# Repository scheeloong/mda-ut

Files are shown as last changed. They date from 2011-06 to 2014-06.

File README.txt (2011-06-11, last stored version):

Directory: root
Use: Holds everything that needs to be held
Author: Mark Harfouche
Editors:

This directory holds all the other directories.
It also has a makefile that, for the sake that if things change

Changes directories, and compiles everything appropriatly.

Things should be compiled in the following order:

SOPC
FPGA
BSP
NIOS2 CODE

VISION

JOYSTICK

...

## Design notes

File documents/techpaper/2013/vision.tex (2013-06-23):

\section{Software}

The vision subsystem is a critical component of AquaTux because it is
the one performing the identification of mission objectives. It is
also complementary to the passive sonar to grab the suitcase above the
acoustic pinger. Because the turbidity of the water and the small
number of visual features in the underwater floor prevent making
reliable correspondences between two views, we decided that stereo
vision was impractical in our vessel. Instead, we use two independent
cameras: one facing forward and one facing down. Since they
are rigidly attached to the AUV, we need to move the AUV
to change the viewpoint. In this section, we explain in more details
the features of our vision subsystem.

\subsection{Software Organization}
\label{gui}

\begin{figure}
\begin{center}
 
\caption{Vision modules organization in the AUV.}\label{vision}
\end{center}
\end{figure}

\begin{figure}
\begin{center}
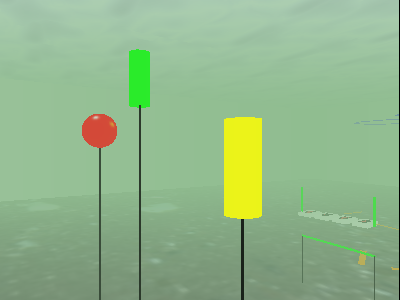
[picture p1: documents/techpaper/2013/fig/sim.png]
 
\caption{Example image from the simulator showing pipe segments, a box
  and a red buoy in turbid water.}\label{sim}
\end{center}
\end{figure}

The vision system is broken down in 3
software components (Figure~\ref{vision}): (i) the mission software that performs the image
processing; (ii) the simulator that recreates synthetic underwater
images based on the vehicle position (example in
Figure~\ref{sim}) and (iii) the graphical interface that is used to
control the mission software. The simulator and the graphical
interface were solely created to test and debug the vision
algorithms when AquaTux is not functioning autonomously. All modules connect through TCP/IP in a
very flexible and extensible fashion. This allows us to seamlessly
replace the simulator by the real hardware sensors and electronics
when we take our system from the lab to the water environment. The
graphical interface allows us to access all the data structures in the
AUV and can act as a passive observer, constantly requesting the
state of the vehicle, or as a controller sending commands to the
vessel.

\vspace{-.1in}
\subsection{Image Processing Software}
The image processing software consists of color filters and edge and
line detection algorithms. The color filters allow us to select
specific information to only process relevant parts of the images. The
line processing algorithms use heuristics to form polygons and
recognize objects such as pipes or boxes, that have a well defined
appearance. Our algorithms are robust enough to recognize objects even
if their view changes due to perspective or the presence of debris in
the water.  The mission software consists of a main loop that acquires
images, processes them and send commands to the other subsystems on
one of the two serial ports of the embedded computer (see
Section~\ref{gui}). The mission is broken down into modular tasks that
can me chained or tested individually. Tasks proceed by first
identifying a target for the vehicle to begin pursuit. If the object
in question is not found, the vehicle rotates on its vertical axis
(yaw) to make the cameras pan to the right and to the left. If nothing
is found, then the vehicle proceeds forward in its initial direction.
Once a target is acquired, the vertical position and lateral positions
of the vessel are controlled to match the desired coordinates.  The
vehicle uses a combination of heading relative to its current
orientation and absolute headings (relative to the magnetic north
pole) to navigate inside the environment. This alleviates the need to
get real-time measurements of the heading as the vehicle is
navigating. A limitation of our vision hardware that we had to address
is to determine when a task is completed if the view of the target is
obscured or occluded due to the AUV's proximity (e.g. it is passing
under the gate). In such situations, for the moment being, we use
timers to ensure that the vehicle reaches its target location.

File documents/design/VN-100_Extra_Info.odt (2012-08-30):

VN-100 Rugged

Useful Information not in manual

The following information was obtained from direct email correspondence between VectorNav and Alex Piggott during the month of August 2012.

CONNECTORS

Connector on the Rugged side: Harwin M80-05001042

Matching connector for the cable: Harwin M80-4861005

These connectors are usually available on Mouser.

QUATERNION CONVENTIONS

The IMU frame is a right-handed coordinate frame with the axes indicated on the VN-100 Rugged case. To map a vector from the world frame into the IMU frame, you would need to convert the quaternion vector into a direction cosine matrix and multiply that DCM into the world frame vector:

DCM(q)*v = V

where:

v = world-frame vector

V = IMU-frame vector

and DCM(q) is defined by:

Note: the above notation has the scalar component of the quaternion denoted by q0, the VectorNav units use q4 as the scalar component.

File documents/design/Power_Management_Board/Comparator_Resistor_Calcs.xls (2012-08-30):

Nominal | Measure | Ratio | Ra | Rb_ideal | Rb_real | Ratio_actual | Trigger_actual | Percent_Trigger
24 | 20 | 0.03 | 100000 | 3092.783505 | 3090 | 0.02997 | 20.02 | -0.1659385113
12 | 12.84 | 0.04672897196 | 100000 | 4901.960784 | 4870 | 0.04644 | 12.92 | 0.07669404517
12 | 11.16 | 0.05376344086 | 100000 | 5681.818182 | 5760 | 0.05446 | 11.02 | -0.08194444444
5 | 5.35 | 0.1121495327 | 100000 | 12631.57895 | 12700 | 0.11269 | 5.32 | 0.06488188976
5 | 4.65 | 0.1290322581 | 100000 | 14814.81481 | 14700 | 0.12816 | 4.68 | -0.06367346939
3.3 | 3.531 | 0.1699235344 | 100000 | 20470.82907 | 20500 | 0.17012 | 3.53 | 0.06873614191
3.3 | 3.069 | 0.1955034213 | 100000 | 24301.33657 | 24300 | 0.19549 | 3.07 | -0.06995884774
Notes:
1) Trigger voltages are +/- 7% of nominal voltages
2) Comparator has 0.6V references
3) Input bias current is 10nA => for <1% error due to input bias currents, require < 600kOhm resistance

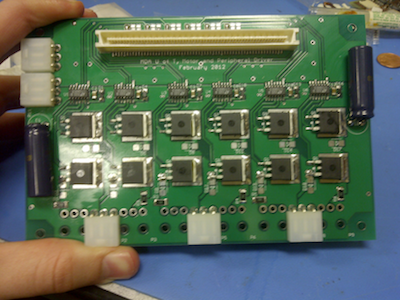
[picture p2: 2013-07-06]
documents/techpaper/2013/fig/motor_board.png

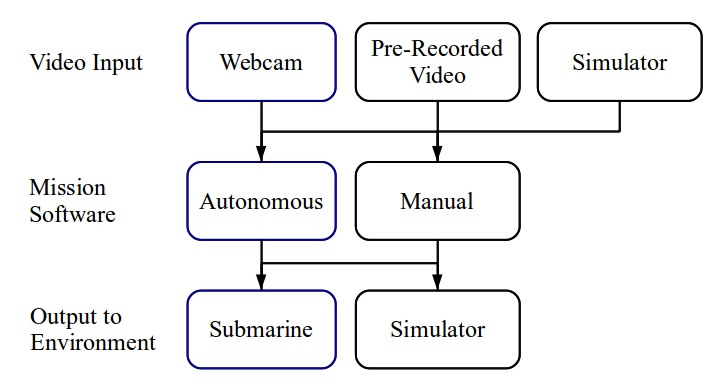
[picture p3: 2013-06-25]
documents/techpaper/2013/fig/modules.png

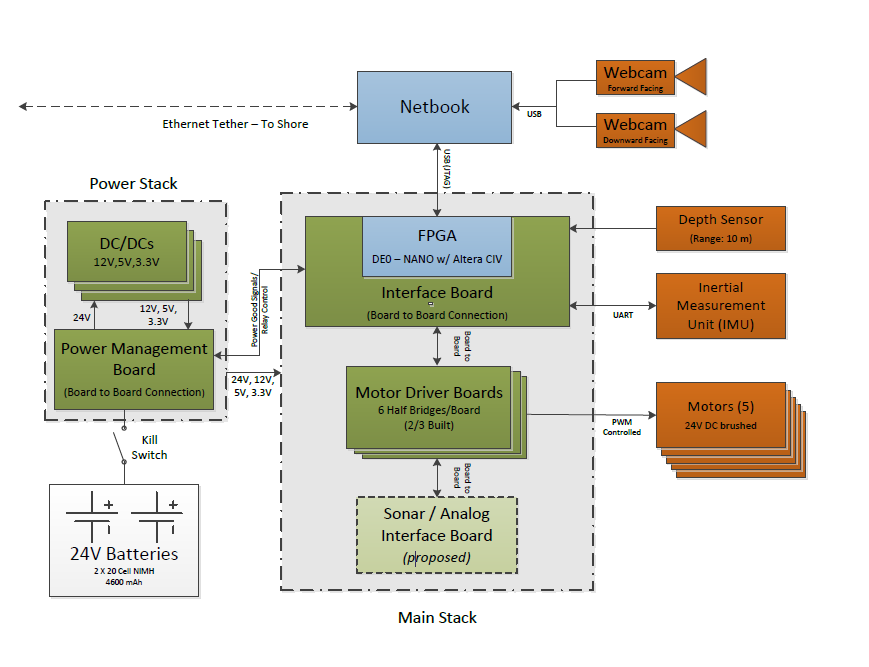
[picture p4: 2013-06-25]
documents/techpaper/2013/fig/arch.png

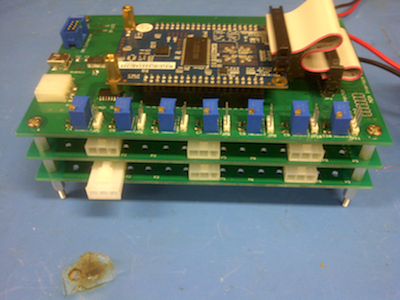
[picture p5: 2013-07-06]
documents/techpaper/2013/fig/main_stack.png

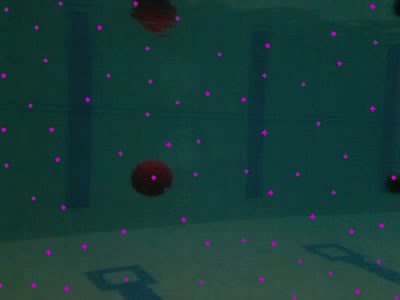
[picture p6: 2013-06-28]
documents/techpaper/2013/fig/seed_image.jpg

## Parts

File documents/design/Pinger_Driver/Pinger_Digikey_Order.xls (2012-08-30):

Digikey PN | Manufacturer PN | Manufacturer | Description | Price | Quantity | Total Cost
285-1893-ND | LS35-24 | TDK-Lambda | 24V @ 1.5A AC-DC Power Supplies | 20.38 | 2 | 40.76
160-1358-5-ND | LTV-815 | LITE-ON | Optoisolator- 1Ch, Darlington Output, 4-DIP | 0.54 | 2 | 1.08
AE10022-ND | AR06-HZL-TT-R | Assmann WSW Components | 6-DIP socket | 0.48 | 2 | 0.96
2N7000TACT-ND | 2N7000TA | Fairchild Semiconductor | MOSFET N-Ch, 60V, 200mA, TO-92 | 0.44 | 2 | 0.88
CH770-ND | LRA32H2FBBNN | Cherry | Switch Rocker DPST 10A 125V | 1.46 | 1 | 1.46
A32340-ND | 5227726-2 | TE Connectivity | BNC Panel-mount jack | 3.50 | 1 | 3.50
A98505-ND | 1546306-4 | TE Connectivity | Barrier strip - 4 x 2 (double row) | 1.53 | 1 | 1.53
708-1329-ND | PF0001/63 | Bulgin | Power entry module with 6.3mm fuse | 3.57 | 1 | 3.57
F4186-ND | 01000058Z | Littelfuse Inc | Fuse clip (1/4") | 0.22 | 10 | 2.18
255-2098-5-ND | ALE14B24 | Panasonic Electric Works | Relay General Purposes SPST 16A 24V | 2.74 | 1 | 2.74
208697-2-ND | 208697-2 | TE Connectivity | Power Outlet Assembly | 1.49 | 1 | 1.49
HM1200-ND | 1550N | Hammond Manufacturing | Box Aluminum 9.85 x 9.85 x 3.99" Natural | 52.34 | 1 | 52.34
F1759-ND | 0312001.MXP | Littelfuse Inc | Fuse 1A 1" x 1 1/4", fast | 0.37 | 6 | 2.22
F1765-ND | 0313001.MXP | Littelfuse Inc | Fuse 1A 1" x 1 1/4", slow | 1.07 | 2 | 2.14
 |  |  |  |  | Shipping | 8.00
 |  |  |  |  | Subtotal | 124.85
 |  |  |  |  | Tax | 16.23
 |  |  |  |  | Total | 141.08

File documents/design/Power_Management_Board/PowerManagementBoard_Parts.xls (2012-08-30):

Description | Manufacturer | Digikey PN | Manufacturer PN | Package | Quantity
Relay (General Purpose), SPST, 30A 24V | Panasonic Electric Works | 255-2818-ND | JTV1AS-PA-24V | Through-Hole | 1
Magnetic Reed Switch | Cherry | CH405-ND | MP201801 |  | 1
Solid State Relay, 300mA, 1.15V input | Omron Electronics Inc-EMC Div | Z157-ND | G3VM-VF | Gull-wing SMD | 1
Comparator (push-pull, active-high, 0.6V ref) | Analog Devices Inc | ADCMP356YKSZ-REEL7CT-ND | ADCMP356YKSZ-REEL7 | SC-70-4 | 7
Multiplexer (8:1, 2-6V supply) | STMicroelectronics | 497-7348-1-ND | M74HC151TTR | 16-TSSOP | 1
N-Ch MOSFET (logic level) | Diodes/Zetex | ZXM61N02FCT-ND | ZXM61N02FTA | SOT-23-3 | 1
Schottky Diode (inductor flyback) | Fairchild Semiconductor | SS16FSDKR-ND | SS16 | DO-214AC, SMA | 3
1uH inductor (shielded SMT, 17A) | Wurth Electronics Inc | 732-2162-1-ND | 7443340100 | SMT | 3
220uF capacitor (35V electrolytic) | Panasonic - ECG | PCE4444CT-ND | EEE-FP1V221AP | SMT | 3
10uF Capacitor (35V, Y5V) | Taiyo Yuden | 587-1352-1-ND | GMK316F106ZL-T | 1206 | 6
1uF Capacitor | N/A - MDA already has stock |  |  | 1206 | 3
220R (Solid-State Relay diode resistor) | N/A - MDA already has stock |  |  |  | 1
1K (FPGA output pull-down resistor) | N/A - MDA already has stock |  |  |  | 1
Terminal Block, 2-pos, 200 mil spacing | TE Connectivity | A98342-ND | 282841-2 | Through hole | 2
Terminal Block, 3-pos, 200 mil spacing | TE Connectivity | A98343-ND | 282841-3 | Through hole | 1
Terminal Block, 5-pos, 200 mil spacing | TE Connectivity | A98082-ND | 282841-5 | Through hole | 1
Comparator Resistors (all 1% precision)
100K | Yageo | 311-100KHRCT-ND | RC0603FR-07100KL | 0603 | 7
3.09k | Yageo | 311-3.09KHRCT-ND | RC0603FR-073K09L | 0603 | 1
4.87K | Yageo | 311-4.87KHRCT-ND | RC0603FR-074K87L | 0603 | 1
5.76K | Yageo | 311-5.76KHRCT-ND | RC0603FR-075K76L | 0603 | 1
12.7K | Yageo | 311-12.7KHRCT-ND | RC0603FR-0712K7L | 0603 | 1
14.7K | Yageo | 311-14.7KHRCT-ND | RC0603FR-0714K7L | 0603 | 1
20.5K | Yageo | 311-20.5KHRCT-ND | RC0603FR-0720K5L | 0603 | 1
24.3K | Panasonic - ECG | P24.3KHCT-ND | ERJ-3EKF2432V | 0603 | 1
Aside (replacement inductor if filtering doesn't work) => DO NOT ORDER THIS PART!
3.3uH inductor (shielded SMT, 14A) | Wurth Electronics Inc | 732-2165-1-ND | 7443340330 | SMT

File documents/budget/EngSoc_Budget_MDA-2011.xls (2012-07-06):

 |  |  | University of Toronto
 |  |  | Engineering Society
 |  |  | Club Budget
 |  |  | Send budgets to Jonathan Ng, Vice-President Finance
 |  |  | at vpfinance@skule.ca or submit to the EngSoc Office (SF B740)
 |  |  | Please accompany this budget with all relevant documents
 |  |  | (including price quotes, further commentaries, and other justifications)
 | Name: | Ritchie Zhao
 | Position: | Treasurer
 | Account/Committee: | Mechatronics Design Association
 | Proposed Net Expenses: | $6047.00 | Date: | 2019-07-01
 | Last Year's Net Expenses: | $1000.00
 | Description of Request/Notes:
 | Revenues
4600 | Expected revenue (selling tickets, fundraisers, etc) and short explanation |  |  | Amount Requested | Amount Approved | Spent to Date | Last Year
1 | Donation request to Altera |  |  | $237 in FPGAs | $237 in FPGAs | Item was donated | N.A.
2 | Funding Request to Division of Engsci |  |  | $1000.00 | $0.00 | $0.00 | $1125.00
3 | Funding Request to Department of ECE |  |  | $1000.00 | $0.00 | $0.00 | $1000.00
4 | Funding Request to Department of MIE |  |  | $1000.00 | $0.00 | $0.00 | $1000.00
5 | U of T Alumini |  |  | $1600.00 | $0.00 | $0.00 | $1600.00
6
7
8
9
10
11
12
13
14
15
16
 |  | Total Expected Revenue |  | $4600.00 | $0.00 | $0.00 | $4725.00
 | Expenses
1637 | Expected expenses (ie supplies, food, etc) and short explanation |  |  | Amount Requested | Amount Approved | Spent to Date | Last Year
1 | Pressure Gauge (air column pressure sensor) |  |  | $100.00
2 | Torpedo Launch Mechanism (compressed air/CO2 mechanism) |  |  | $200.00
3 | Vacuum Pump (to test hull integrity outside of water) |  |  | $350.00 |  |  |  | http://www.labwrench.com/
4 | Object Dropper (mechanism built. Need drivers) |  |  | $50.00 |  |  |  | Just need the driver board
5 | Manipulator Arm (arm to grab an object) |  |  | $200.00
6
7 | Onboard Computer (small cheap used netbook) |  |  | $500.00 |  |  |  | Find on Ebay/Craigslist
8 | Altera FPGAs (DE0 boards) |  |  | $237.00 | $237.00 | $237.00 | $0.00 | Donated by altera
9 | Wires and Connectors () |  |  | $100.00 |  |  | $400.00 | Last years were rubber waterproof ones
10 | Machine Vision Cameras |  |  | $100.00 |  |  |  | 2 of Logitech webcam c905, quickcam pro, or webcam pro9000, used. http://www.amazon.com/gp/offer-listing/B000RZQZM0?s=electronics&condition=used
11 | Hydrophone Boards |  |  | $250.00 |  |  |  | http://www.quickfiltertech.com/html/content_page.php?content_id=8&
12 | Depth Sensor |  |  | $100.00
13 | Inertial Measurement Unit (gyroscopes and accelerometers package) |  |  | $300.00 |  |  |  | http://www.pnicorp.com/products/prime
14 | Motor Controllers |  |  | $700.00 |  |  |  | We have detail calculations for this
15 | Battery Chargers |  |  | $100.00
16
17 | Pool Test Time |  |  | $750.00 |  |  |  | In previous years athletic center offered $75 per hour.
18 | Obstacle Course Materials (PVC piping of different colors, plexiglass boards, bouys, paint) |  |  | $100.00
19 | Contest Fee |  |  | $500.00 |  |  |  | http://www.auvsifoundation.org/AUVSI/FOUNDATION/Competitions/RoboSub/RoboSubOverview/Default.aspx
20 | Vehicle Shipment |  |  | $450.00 |  |  |  | To san diego and back. The vehicle is about 50cm x 40cm x 25cm and at least 30 kg.
21 | Van Rental for Transport (6 to 7 days) |  |  | $600.00 |  |  |  | budget, thrifty, etc. Need an SUV. Includes gas.
22
23 | Hull Mechanical Parts |  |  | $0.00 | $0.00 | $0.00 | $200.00
24 | Sonar DSP Board |  |  | $0.00 | $0.00 | $0.00 | $200.00
25 | Active Electronic Components (microcontrollers, chips) |  |  | $0.00 | $0.00 | $0.00 | $200.00
26 | Recruitment events and social outings |  |  | $300.00 |  |  |  | $100 for pizza at the recruitment event, $200 for a bar social
27
28 | Contingency (please budget 5% on unknown costs) |  |  | $0.00 | $0.00 | $0.00 | $0.00 | Our cost estimates already have a margin of error, this seems unecessary
 | Subtotal |  |  | $5987.00 | $237.00 | $237.00 | $1000.00
 | HST (13%) |  |  | $0.00 | $0.00 | $0.00 | $0.00 | Again, this is mostly accounted for.
 |  | Total Expected Expenses |  | $5987.00 | $237.00 | $237.00 | $1000.00
 | Reserved for Finance Committee
 | Outcome: | o Approved |  | o Returned
 | Recommended Funding:
 | Notes:

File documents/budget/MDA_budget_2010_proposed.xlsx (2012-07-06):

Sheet: Sheet1
 | Expected Expenses | Unit cost | Units | Total | Envisionned Sponsor
Mechanical | Pelican Case for new Hull | $75.00 | 1 | $75.00 | UofT Department of Mechanical and Industrial Engineering
 | Vehicle material - Polycarbonate, PVC, aluminum | $300.00 | 1 | $300.00
 | Mechanical Grabber | $250.00 | 1 | $250.00
 | Fabrication Cost | $400.00 | 1 | $400.00
 | Torpedo ammo, plastic prototyped | $100.00 | 4 | $400.00 | Proto3000
 | Fabrication tools | $300.00 | 1 | $300.00 | Black & Decker
 | Torpedo actuation Mechanism | $150.00 | 2 | $300.00 | UofT Rogers Department of Electrical and Computer Engineering
Electrical | Passive electronic devices (resistors, capacitors, diodes, switches, relays) | $100.00 | 1 | $100.00 | 15% off from Digikey, UofT Rogers Department of Electrical and Computer Engineering
 | Active devices - micro controllers, amplifiers, voltage regulators, MOSFETs | $500.00 | 1 | $500.00
 | Wires and connectors | $100.00 | 1 | $100.00
 | Waterproof connectors | $100.00 | 4 | $400.00 | Teledyne Impulse Ent.
 | Digital multimeter | $150.00 | 2 | $300.00 | Fluke Corporation
 | Digital osciloscope | $950.00 | 1 | $950.00 | LeCroy
 | Printed Circuit Boards | $400.00 | 1 | $400.00 | Coretec Inc.
 | On-board netbook | $600.00 | 1 | $600.00 | Lenovo
Testing | Devellopment computer | $500.00 | 1 | $500.00
 | Pool time | $75.00 | 15 | $1125.00 | UofT Division of Engineering Science
 | PVC | $200.00 | 1 | $200.00 | University of Toronto Engineering Society
Competition costs | Contest entrance fee | $500.00 | 1 | $500.00
 | Shipment of tools and vehicle to and from San Diego | $1000.00 | 1 | $1000.00 | UofT Engineering Alumni
 | Ten day van rental in San Diego for transporting the vehicle to and from the hotel to the competition | $600.00 | 1 | $600.00
 |  |  | Total | $9300.00

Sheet: Sheet2
Subsystem | Description | Paid in 2008-2009 | Funding 2008-2009 | Expected Expense 2010-2011 | Funding Source 2010 - 2011
Mechanical | Pellican case for new hull | N/A | New addition in 2010/2011 | $75 | UofT Department of Mechanical and Industrial Engineering
 | PVC for frame | $200 | Office of the Provost | $150 | UofT Department of Mechanical and Industrial Engineering
 | Plastic for the hull | $100 | Office of the Provost | N/A | The new null is to use the pellican case
 | Aluminium for hull | $50 | Office of the Provost | $150 | UofT Department of Mechanical and Industrial Engineering
 | Mechanical Grabber | N/A | New addition in 2010/2011 | $250 | UofT Department of Mechanical and Industrial Engineering
 | Fabrication Costs | $300 | Retained Funds | $400 | UofT Department of Mechanical and Industrial Engineering
 | Torpedo ammo | N/A | New addition in 2010/2011 | $400 | Proto3000
 | Fabrication Tools | $400 | Black and Decker | $300 | Black and Decker
 | Torpedo actuation mechanism | N/A | New addition in 2010/2011 | $300 | Department of Electrical and Computer Engineering
Electrical | Passive electronic devices (resistors, capacitors, diodes, switches, relays) | $100 | 15% off Digikey, Department of Electrical and Computer Engineering | $100 | 15% off Digikey, Department of Electrical and Computer Engineering
 | Active devices - micro controllers, amplifiers, voltage regulators, MOSFETs | $600 | 15% off Digikey, Department of Electrical and Computer Engineering | $500 | 15% off Digikey, Department of Electrical and Computer Engineering
 | Wires | $50 | 15% off Digikey, Department of Electrical and Computer Engineering | $50 | 15% off Digikey, Department of Electrical and Computer Engineering
 | Connectors | $40 | 15% off Digikey, Department of Electrical and Computer Engineering | $50 | 15% off Digikey, Department of Electrical and Computer Engineering
 | Waterproof connectors | N/A | Needed for new actiontion mechanisms in 2010/2011 | $400 | Teledyne Impulse Ent.
 | Digital Multimeters | N/A | Borrowed from club members | $300 | Fluke Corporation
 | Variable voltage power supplies | $300 | Donation from the UofT ECE labs | N/A | Using old power supplies
 | Printed circuit boards | $400 | Deparetment of Electrical and Computer Engineering | $400 | Coretec Inc.
 | On board computer | N/A | The old computer was still functional | $600 | Lenovo Inc.
 | Digital Osciloscope | N/A | Using a previously donated analog osciloscope | $950 | LeCroy
Testing | Devellopment Computers | N/A | Using old computers | $500 | Lenovo Inc.
 | Pool time | N/A | Used the condo pool of a club member, this year, it was decided that the depth of this pool is no longer sufficient for our testing purposes | $1125 | UofT Division of Engineering Science
 | PVC | N/A | We did not build testing equipment this year | $200 | UofT Engineering Society
Competition Cost | Contest entrance fee | $500 | Alumni funding | $500 | UofT Engineering Society
 | Shipping | $800 | Division of Engineering Science + Alumni funding | $1000 | Alumni
 | Ten day van rental | N/A | A club member had a PEY job near San Diego and donated his car and gas for the competition | $600 | Alumni
 | Total | $3840 |  | $9300
Notes
 | Club activity was suspended during the year of 2009-2010 due to the fact that most club veterans were involved in other activities, Figures from 2008-2009 are shown instead.
 | Note increase in budget comes from envisionned corporate sponsors that would mainly donate testing and debugging equipment. The increase in members interested in contacting external companies has allowed us to be hopeful in obtaining the donated items. We have also had a great increase in members from the Department of Mechanical and Industrial Engineering which has allowed us to ask the Department for funding. Due to the increase in members interested in contacting sponsors, we are also requesting funding from the Engineering Society, a source that was not approached in the past.

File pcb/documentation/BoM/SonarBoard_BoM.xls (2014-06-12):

Code_IEC | Code_IPC | Code_JEDEC | Code_JEITA | Comment | ComponentAvailability | Datasheet | Description | Designator | Digikey PN | Footprint | LibRef | Quantity | Value
 |  |  |  | AD7264 |  | http://www.analog.com/static/imported-files/data_sheets/AD7264.pdf | AD7264 - 14 bit 1MSPS 2 channel ADC | ADC1_1, ADC1_2 |  | TSQFP50P900X900-48N | AD7264 | 2
 |  |  |  | Cap Semi |  |  | Capacitor (Semiconductor SIM Model) | C1_1, C1_2, C1_3, C1_4, C3_1, C3_2, C4_1, C4_2, C5_1, C5_2, C6_1, C6_2, C7_1, C7_2, C8_1, C8_2, C9_1, C9_2, C10_1, C10_2, C11_1, C11_2, C11_3, C11_4, C12_1, C12_2, C12_3, C12_4, C13_1, C13_2, C13_3, C13_4, C14_1, C14_2, C14_3, C14_4, C16_1, C16_2, C16_3, C16_4, C17_1, C17_2, C17_3, C17_4, C18, C21, C24, C25, C26, C27, C28, C29, C30, C31 |  | C0805 | Cap Semi | 55 | 1nF, 10nF, 10uF, 100nF
 |  |  |  | Cap Semi |  |  | Capacitor (Semiconductor SIM Model) | C2_1, C2_2, C2_3, C2_4, C15_1, C15_2, C15_3, C15_4 |  | C1206 | Cap Semi | 8 | 10uF
 |  |  |  | Cap Pol3 |  |  | Polarized Capacitor (Surface Mount) | C22, C23 | 718-1052-6-ND, 718-1077-1-ND | TC6032-2412 | Cap Pol3 | 2 | 10uF, 33uF
 |  |  |  | Cap Pol3 |  |  | Polarized Capacitor (Surface Mount) | C24 |  | TC3216-1206 | Cap Pol3 | 1 | 10uF
 |  |  |  | Shottkey |  |  | Schottky Rectifier | D1 | B340A-FDICT-ND | TO-220AC | Diode 10TQ035 | 1
 |  |  |  | D Zener |  |  | Zener Diode | D2, D3, D4, D5, D6, D7, D8, D9 |  | SOD-323 | D Zener | 8
1005 |  |  | 0402 | Inductor |  |  | Inductor | L1 | 495-1987-1-ND | SB_IND | Inductor | 1 | 100uH
 |  |  |  | 120P_SMD_CONN_FEM |  | http://www.hirose.co.jp/cataloge_hp/e57220088.pdf | Main Stack Connector, Female | MS_T1, MSB1 |  | FX2-120P-1.27SV | 120P_SMD_CONN_FEM | 2
 |  |  |  | SMB |  |  | SMB Straight Connector | P1_1, P1_2, P1_3, P1_4 | WM5534-ND | SMA_SMT | SMB | 4
 |  |  |  | Header 5H |  |  | Header, 5-Pin, Right Angle | P2 |  | Molex_Minifit_JR_5CKT | Header 5H | 1
 |  |  |  | Header 10 |  |  | Header, 10-Pin | P3 |  | Harwin_IMU_recp | Header 10 | 1
 |  |  |  | Header 3H |  |  | Header, 3-Pin, Right Angle | P4, P5, P6, P7 |  | HDR1X3H | Header 3H | 4
 |  |  |  | Res Semi |  |  | Semiconductor Resistor | R1_1, R1_2, R1_3, R1_4, R2_1, R2_2, R2_3, R2_4, R3_1, R3_2, R3_3, R3_4, R4_1, R4_2, R4_3, R4_4, R5_1, R5_2, R5_3, R5_4, R6, R6_1, R6_2, R6_3, R6_4, R7, R7_1, R7_2, R7_3, R7_4, R8, R8_1, R8_2, R8_3, R8_4, R12, R13, R14, R15, R16, R17, R18, R19, R20, R21, R22, R23, R24, R25, R26, R27 |  | 6-0805_M | Res Semi | 51 | 1K, 1M, 2K, 3K, 5K, 7K, 10K, 15K, 18K, 20K, 100K
 | SOIC127P600-8 | MS-012-AA |  | OP184ES |  |  | Precision Rail-to-Rail Input and Ouput Operational Amplifier | U1_1, U1_2, U1_3, U1_4, U3_1, U3_2, U3_3, U3_4 | OP184FSZ-REEL7CT-ND | SO-8 | OP184ES | 8
 |  |  |  | ADA4899 |  | http://www.analog.com/static/imported-files/data_sheets/ADA4899-1.pdf | High Speed, Low Voltage Noise, Unity Gain Stable Op-Amp | U2_1, U2_2, U2_3, U2_4 |  | SO8_N | ADA4899 | 4
 | SOIC127P1030-20 | MS-013 |  | SN74BCT541DW | Obsolete | http://www.ti.com/lit/ds/symlink/sn74bct541a.pdf | Octal Buffer/Driver with 3-State Outputs | U4 | 296-33840-5-ND | DW020 | SN74BCT541DW | 1
 |  |  |  | TPS5420 |  | http://www.ti.com/lit/ds/symlink/tps5420.pdf | 2A Wide Input Range Step-Down Swift Converter | U4 | 296-19671-5-ND | SO8_M | TPS5420 | 1
 |  |  |  | LP3852 |  | http://www.ti.com/lit/ds/symlink/lp3852.pdf | 1.5A Fast Response Ultra Low Dropout Linear Regulator | U5 | LP3852EMP-5.0/NOPBCT-ND | SOT223-5N | LP3852 | 1

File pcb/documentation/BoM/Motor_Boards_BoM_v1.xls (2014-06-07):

 |  | *Quantities are exact
Digikey Part No. | Description | Quantity:
IPB70N04S3-07CT-ND | Mosfets | 36
RMCF2010JT1K50CT-ND | Power Pull-Downs (3/4W) | 18
WM18434-ND | Molex 3ckt Recept. | 24
WM18446-ND | Molex 3ckt Header | 24
1N4148W-FDICT-ND | 1N4148 for Charge Pump | 18
MBRS140FSCT-ND | Shottkey Power Flybacks | 18
P11260-ND | Electrolytic Caps | 6
587-1352-1-ND | 10 uF, 1206 caps | 18
 | 1 uF, 1206 caps | 18 | We alread have these
LT1160CS#PBF-ND | Half Bridge Drivers | 18 | <- Get the price break at 25
Please add approriate numbers of main stack connectors: one mating pair per board.

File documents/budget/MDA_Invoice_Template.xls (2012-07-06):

 |  | INVOICE
Mechatronics Design Association
Engineering Society - University of Toronto
 |  | DATE:
10 King's College Road Suite B740 |  | 2011-07-27
Toronto, Ontario M5S 3G4
Phone 123-456-7890 |  | INVOICE #
 |  | 2011-001
Bill To: | For:
Mechatronics Design Association | KBC Tools Equipment
DESCRIPTION |  | AMOUNT
Mechanical tools and equipment bought from KBC, see attached sales reciept |  | $209.36
Same as above |  | 86.87
 | SUBTOTAL | $296.23
 | TAX RATE
 | TOTAL | $296.23
Make all checks payable to Mechatronics Design Association
If you have any questions concerning this invoice, contact:
Ritchie Zhao (Treasurer) at 416-272-8076 or ritchie.zhao@utoronto.ca

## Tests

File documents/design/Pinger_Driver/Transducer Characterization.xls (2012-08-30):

Frequency (KHz) | V_total (Vpp) | V_resistor (Vpp) | Z (assume reactive) | Z (assume resistive) | Z_ideal (10nF capacitor)
11.06 | 4.20 | 0.54 | 1542.6 | 1355.6 | 1439.0 | Capacitive
12.74 | 4.24 | 0.62 | 1353.0 | 1167.7 | 1249.3 | Capacitive
14.08 | 4.20 | 0.70 | 1183.2 | 1000.0 | 1130.4 | Capacitive
16.90 | 4.16 | 0.84 | 970.1 | 790.5 | 941.7 | Capacitive
19.03 | 4.16 | 0.94 | 862.2 | 685.1 | 836.3 | Capacitive
21.79 | 4.12 | 1.08 | 736.3 | 563.0 | 730.4 | Capacitive
24.50 | 4.08 | 1.22 | 638.3 | 468.9 | 649.6 | Capacitive
27.00 | 4.08 | 1.42 | 538.7 | 374.6 | 589.5 | Capacitive
29.20 | 3.96 | 1.60 | 452.8 | 295.0 | 545.1 | Capacitive
30.30 | 3.72 | 1.70 | 389.3 | 237.6 | 525.3 | Capacitive / Resistive
30.74 | 3.64 | 1.28 | 532.4 | 368.8 | 517.7 | Capacitive / Resistive
31.50 | 3.76 | 0.90 | 811.3 | 635.6 | 505.3 | Capacitive / Resistive
33.10 | 3.76 | 1.20 | 593.9 | 426.7 | 480.8 | Capacitive / Resistive
34.40 | 3.76 | 1.16 | 616.7 | 448.3 | 462.7 | Capacitive
36.13 | 3.76 | 1.32 | 533.4 | 369.7 | 440.5 | Capacitive
38.00 | 3.76 | 1.40 | 498.5 | 337.1 | 418.8 | Capacitive
40.40 | 3.68 | 1.56 | 427.3 | 271.8 | 393.9 | Capacitive
Measurement Details
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

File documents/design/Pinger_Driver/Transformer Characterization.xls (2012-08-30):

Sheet: Transformer Output Ratio
Frequency (kHz) | Primary (Vpp) | Secondary (Vpp) | Voltage Ratio
12.2 | 3.22 | 19.4 | 6.02
14.0 | 3.22 | 19.4 | 6.02
16.8 | 3.24 | 19.6 | 6.05
19.9 | 3.24 | 19.4 | 5.99
22.2 | 3.24 | 19.4 | 5.99
24.6 | 3.24 | 19.4 | 5.99
27.0 | 3.24 | 19.6 | 6.05
29.5 | 3.26 | 19.6 | 6.01
32.0 | 3.26 | 19.6 | 6.01
34.5 | 3.26 | 19.6 | 6.01
37.5 | 3.28 | 19.6 | 5.98
40.2 | 3.28 | 19.6 | 5.98
 |  | Average | 6.01
Measured with an OPEN load
Frequency response of transformer is almost perfectly flat.
Design voltage ratio is exactly 6.00; measured voltage is exactly as predicted

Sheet: Primary Imped - Open Secondary
Frequency (kHz) | V_total (Vpp) | V_resistor (mVpp) | Z_primary (ohms)
11.7 | 3.42 | 158 | 432.4491573
14.6 | 3.44 | 120 | 572.9843899
18.4 | 3.44 | 86 | 799.7499609
21.7 | 3.43 | 62.6 | 1095.664123
23.78 | 3.42 | 51.0 | 1341.027339
26.74 | 3.5 | 38.8 | 1804.012851
30.49 | 3.5 | 23.0 | 3043.412546
33.1 | 3.48 | 13.9 | 5007.154302
37.3 | 3.32 | 6.4 | 10374.98072
39.3 | 3.32 | 8.8 | 7545.428039
41.7 | 3.4 | 14.6 | 4657.491305
Placed 20ohm resistor in series with primary (fewer turns), OPEN secondary
Measured voltage across:
 | 1) Resistor
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

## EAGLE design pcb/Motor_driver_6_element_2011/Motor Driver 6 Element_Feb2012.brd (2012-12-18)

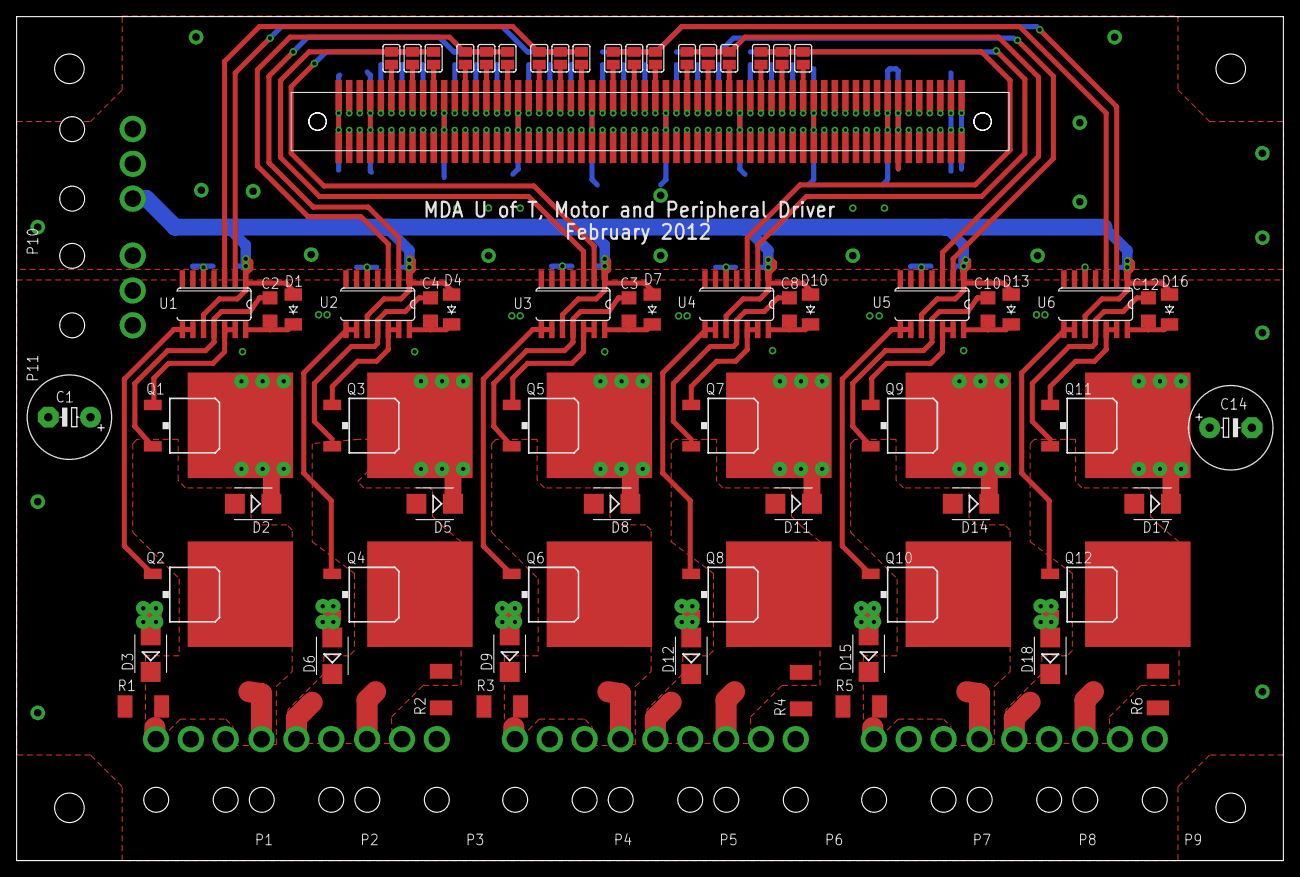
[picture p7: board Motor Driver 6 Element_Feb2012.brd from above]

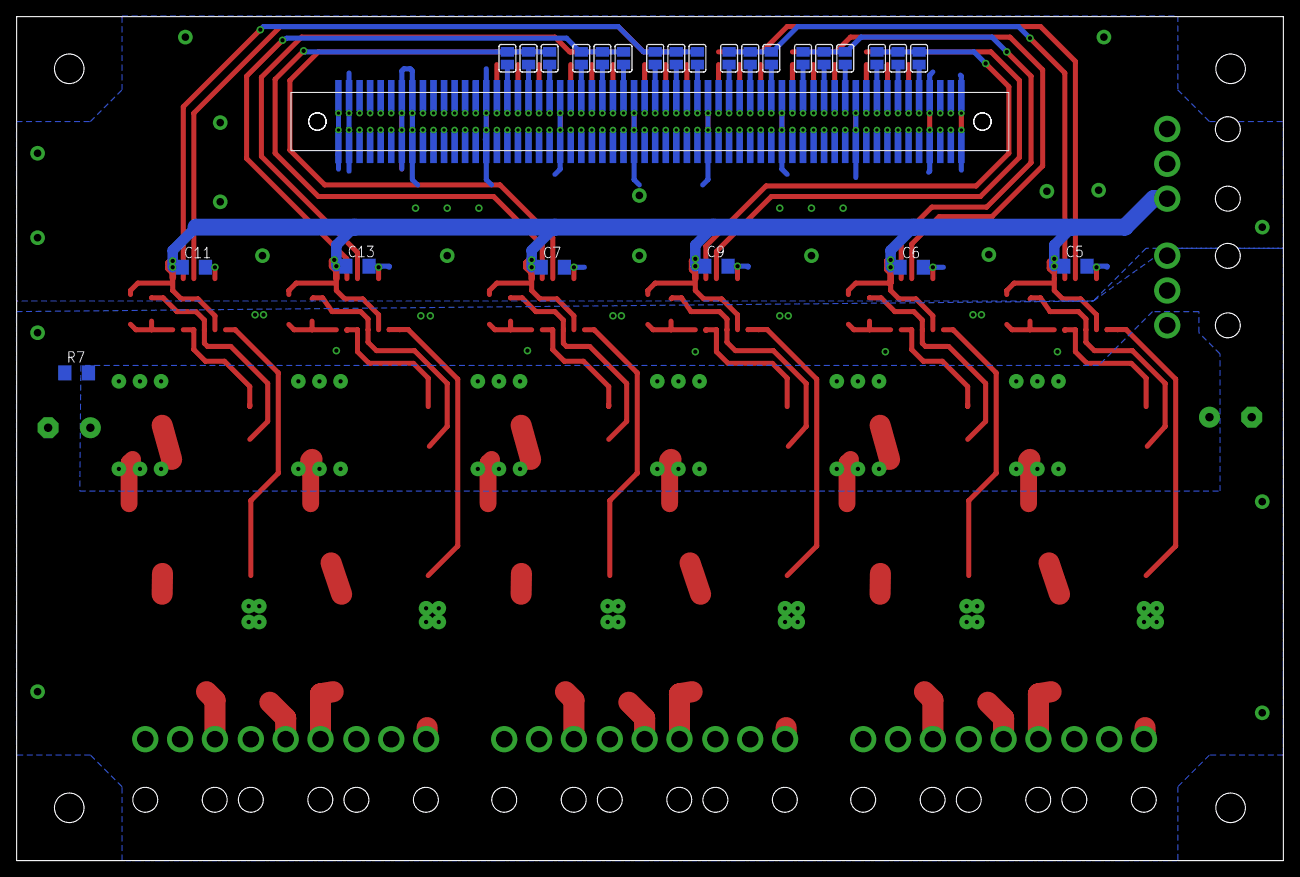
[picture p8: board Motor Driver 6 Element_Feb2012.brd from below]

Board: 2 copper layers, 152.4 x 101.5 mm, 106 parts (26 on the bottom side), 136 nets.

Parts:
C1, C14: >100uF; E5-10,5
C2, C3, C4, C8, C10, C12: 1uF; C1206
C5, C6, C7, C9, C11, C13: 10uF; C1206@1
D1, D4, D7, D10, D13, D16: CGRM4001-G; SOD-123_MINI-SMA
D2, D3, D5, D6, D8, D9, D11, D12, D14, D15, D17, D18: SMB
E$1, E$2: STACK-CONN-WIDEPITCH
P1, P2, P3, P4, P5, P6, P7, P8, P9, P10, P11: MOLEX_MINIFIT_JR_3CKT; 3CKT_MINIFIT_JR
Q1, Q2, Q3, Q4, Q5, Q6, Q7, Q8, Q9, Q10, Q11, Q12: IPB70N04S3; D-PAK_TO252AA
R1, R2, R3, R4, R5, R6: 1.5k; R2010
R7: R1206
SJ1, SJ2, SJ3, SJ4, SJ5, SJ6, SJ7, SJ8, SJ9, SJ10, SJ11, SJ12, SJ13, SJ14, SJ15, SJ16, SJ17, SJ18, SJ19, SJ21, SJ22, SJ23, SJ24, SJ25, SJ26, SJ27, SJ28, SJ29, SJ30, SJ31, SJ32, SJ33, SJ34, SJ35, SJ36, SJ37: SJ
U1, U2, U3, U4, U5, U6: LT1160CS; SOIC14

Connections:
+12V: C5.1, C6.1, C7.1, C9.1, C11.1, C13.1, D1.A, D4.A, D7.A, D10.A, D13.A, D16.A, P10.3, U1.1, U1.10, U2.1, U2.10, U3.1, U3.10, U4.1, U4.10, U5.1, U5.10, U6.1, U6.10
+24V: C1.+, C14.+, P11.3, R7.2
AGND: C1.-, C14.-, D3.A, D6.A, D9.A, D12.A, D15.A, D18.A, P1.3, P3.3, P4.3, P6.3, P7.3, P9.3, P11.2, Q2.3, Q4.3, Q6.3, Q8.3, Q10.3, Q12.3, R1.1, R2.1, R3.1, R4.1, R5.1, R6.1, R7.1, U1.6, U2.6, U3.6, U4.6, U5.6, U6.6
GND: C5.2, C6.2, C7.2, C9.2, C11.2, C13.2, E$1.A1, E$1.A2, E$1.A7, E$1.A8, E$1.A15, E$1.A22, E$1.A29, E$1.A36, E$1.A43, E$1.A50, E$1.A57, E$1.A60, E$1.B1, E$1.B2, E$1.B7, E$1.B8, E$1.B15, E$1.B22, E$1.B29, E$1.B36, E$1.B43, E$1.B50, E$1.B57, E$1.B60, E$2.A1, E$2.A4, E$2.A11, E$2.A18, E$2.A25, E$2.A32, E$2.A39, E$2.A46, E$2.A53, E$2.A54, E$2.A60, E$2.B1, E$2.B4, E$2.B11, E$2.B18, E$2.B25, E$2.B32, E$2.B39, E$2.B46, E$2.B53, E$2.B54, E$2.B59, E$2.B60, U1.5, U2.5, U3.5, U4.5, U5.5, U6.5
unnamed: C2.1, D1.C, U1.14
unnamed: SJ5.2, SJ6.2, SJ7.2, U3.3
unnamed: C3.1, D7.C, U3.14
unnamed: SJ2.2, SJ3.2, SJ4.2, U3.2
unnamed: SJ17.2, SJ18.2, U1.3
unnamed: Q1.1, U1.12, U1.13
unnamed: Q5.1, U3.12, U3.13
unnamed: C8.1, D10.C, U4.14
unnamed: Q8.1, U4.8, U4.9
unnamed: SJ21.2, U4.2
unnamed: SJ22.2, SJ23.2, SJ24.2, U4.3
unnamed: Q7.1, U4.12, U4.13
unnamed: C10.1, D13.C, U5.14
unnamed: SJ25.2, SJ26.2, SJ27.2, U5.3
unnamed: Q9.1, U5.12, U5.13
unnamed: C12.1, D16.C, U6.14
unnamed: Q12.1, U6.8, U6.9
unnamed: SJ31.2, SJ32.2, U6.3
unnamed: Q11.1, U6.12, U6.13
unnamed: C4.1, D4.C, U2.14
unnamed: Q4.1, U2.8, U2.9
unnamed: SJ9.2, SJ10.2, U2.2
unnamed: SJ12.2, SJ13.2, SJ14.2, U2.3
unnamed: Q3.1, U2.12, U2.13
unnamed: SJ1.2, SJ8.2, SJ15.2, U1.2
OUTA: C2.2, D2.A, D3.C, P1.1, P2.1, Q1.3, Q2.4, R1.2, U1.11
OUTA1: C3.2, D8.A, D9.C, P4.1, P5.1, Q5.3, Q6.4, R3.2, U3.11
OUTA2: C10.2, D14.A, D15.C, P7.1, P8.1, Q9.3, Q10.4, R5.2, U5.11
OUTB: C4.2, D5.A, D6.C, P2.2, P3.1, Q3.3, Q4.4, R2.2, U2.11
OUTB1: C8.2, D11.A, D12.C, P5.2, P6.1, Q7.3, Q8.4, R4.2, U4.11
OUTB2: C12.2, D17.A, D18.C, P8.2, P9.1, Q11.3, Q12.4, R6.2, U6.11
S$5: E$1.B55, E$2.B6, SJ7.1
S$6: Q2.1, U1.8, U1.9
S$11: Q6.1, U3.8, U3.9
S$12: E$1.B53, E$2.B8, SJ6.1
S$17: Q10.1, U5.8, U5.9
S$18: E$1.B51, E$2.B10, SJ5.1
S$19: E$1.B48, E$2.B13, SJ14.1
S$20: E$1.B46, E$2.B15, SJ13.1
S$21: E$1.B44, E$2.B17, SJ12.1
S$22: E$1.B41, E$2.B20, SJ18.1
S$23: E$1.B39, E$2.B22, SJ17.1
S$24: E$1.B37, E$2.B24
S$25: E$1.B34, E$2.B27, SJ33.1
S$26: E$1.B32, E$2.B29, SJ32.1
S$27: E$1.B30, E$2.B31, SJ31.1
S$28: E$1.B27, E$2.B34, SJ27.1
S$29: E$1.B25, E$2.B36, SJ26.1
S$30: E$1.B23, E$2.B38, SJ25.1
S$31: E$1.B20, E$2.B41, SJ24.1
S$32: E$1.B18, E$2.B43, SJ23.1
S$33: E$1.B16, E$2.B45, SJ22.1
S$34: E$1.B21, E$2.B40, SJ21.1
S$35: E$1.B19, E$2.B42, SJ19.1
S$36: E$1.B17, E$2.B44, SJ37.1
S$37: E$1.B24, E$2.B37, SJ30.1
S$38: E$1.B26, E$2.B35, SJ29.1
S$39: E$1.B28, E$2.B33, SJ28.1
S$40: E$1.B31, E$2.B30, SJ36.1
S$41: E$1.B33, E$2.B28, SJ35.1
S$42: E$1.B35, E$2.B26, SJ34.1
S$43: E$1.B38, E$2.B23, SJ15.1
S$44: E$1.B40, E$2.B21, SJ8.1
S$45: E$1.B42, E$2.B19, SJ1.1
S$46: E$1.B49, E$2.B12, SJ9.1
S$47: E$1.B47, E$2.B14, SJ10.1
S$48: E$1.B45, E$2.B16, SJ11.1
S$49: E$1.B52, E$2.B9, SJ4.1
S$50: E$1.B54, E$2.B7, SJ3.1
S$51: E$1.B56, E$2.B5, SJ2.1
S$53: SJ34.2, SJ35.2, SJ36.2, U6.2
S$54: SJ28.2, SJ29.2, SJ30.2, U5.2
S$57: E$1.A59, E$2.A2
S$58: E$1.A58, E$2.A3
S$60: E$1.A55, E$2.A6
S$61: E$1.A56, E$2.A5
S$62: E$1.A54, E$2.A7
S$63: E$1.A53, E$2.A8
S$64: E$1.A52, E$2.A9
S$65: E$1.A51, E$2.A10
S$67: E$1.A49, E$2.A12
S$68: E$1.A48, E$2.A13
S$69: E$1.A47, E$2.A14
S$70: E$1.A46, E$2.A15
S$71: E$1.A45, E$2.A16
S$72: E$1.A44, E$2.A17
S$74: E$1.A42, E$2.A19
S$75: E$1.A41, E$2.A20
S$76: E$1.A40, E$2.A21
S$77: E$1.A38, E$2.A23
S$78: E$1.A39, E$2.A22
S$79: E$1.A37, E$2.A24
S$81: E$1.A34, E$2.A27
S$82: E$1.A35, E$2.A26
S$83: E$1.A33, E$2.A28
S$84: E$1.A32, E$2.A29
S$85: E$1.A31, E$2.A30
S$86: E$1.A30, E$2.A31
S$88: E$1.A28, E$2.A33
S$89: E$1.A27, E$2.A34
S$90: E$1.A25, E$2.A36
S$91: E$1.A26, E$2.A35
S$92: E$1.A23, E$2.A38
S$93: E$1.A24, E$2.A37
S$95: E$1.A20, E$2.A41
S$96: E$1.A21, E$2.A40
S$97: E$1.A19, E$2.A42
S$98: E$1.A18, E$2.A43
S$99: E$1.A16, E$2.A45
S$100: E$1.A17, E$2.A44
S$102: E$1.A14, E$2.A47
S$103: E$1.A13, E$2.A48
S$104: E$1.A11, E$2.A50
S$105: E$1.A12, E$2.A49
S$106: E$1.A10, E$2.A51
S$107: E$1.A9, E$2.A52
S$109: E$1.A6, E$2.A55
S$111: E$1.A4, E$2.A57
S$112: E$1.A5, E$2.A56
S$113: E$1.A3, E$2.A58
S$117: E$1.B59, E$2.B2
S$119: E$1.B58, E$2.B3
S$126: E$1.B13, E$2.B48
S$127: E$1.B14, E$2.B47
S$128: E$1.B11, E$2.B50
S$129: E$1.B12, E$2.B49
S$130: E$1.B10, E$2.B51
S$132: E$1.B9, E$2.B52
S$133: E$1.B6, E$2.B55
S$135: E$1.B5, E$2.B56
S$136: E$1.B4, E$2.B57
S$137: E$1.B3, E$2.B58

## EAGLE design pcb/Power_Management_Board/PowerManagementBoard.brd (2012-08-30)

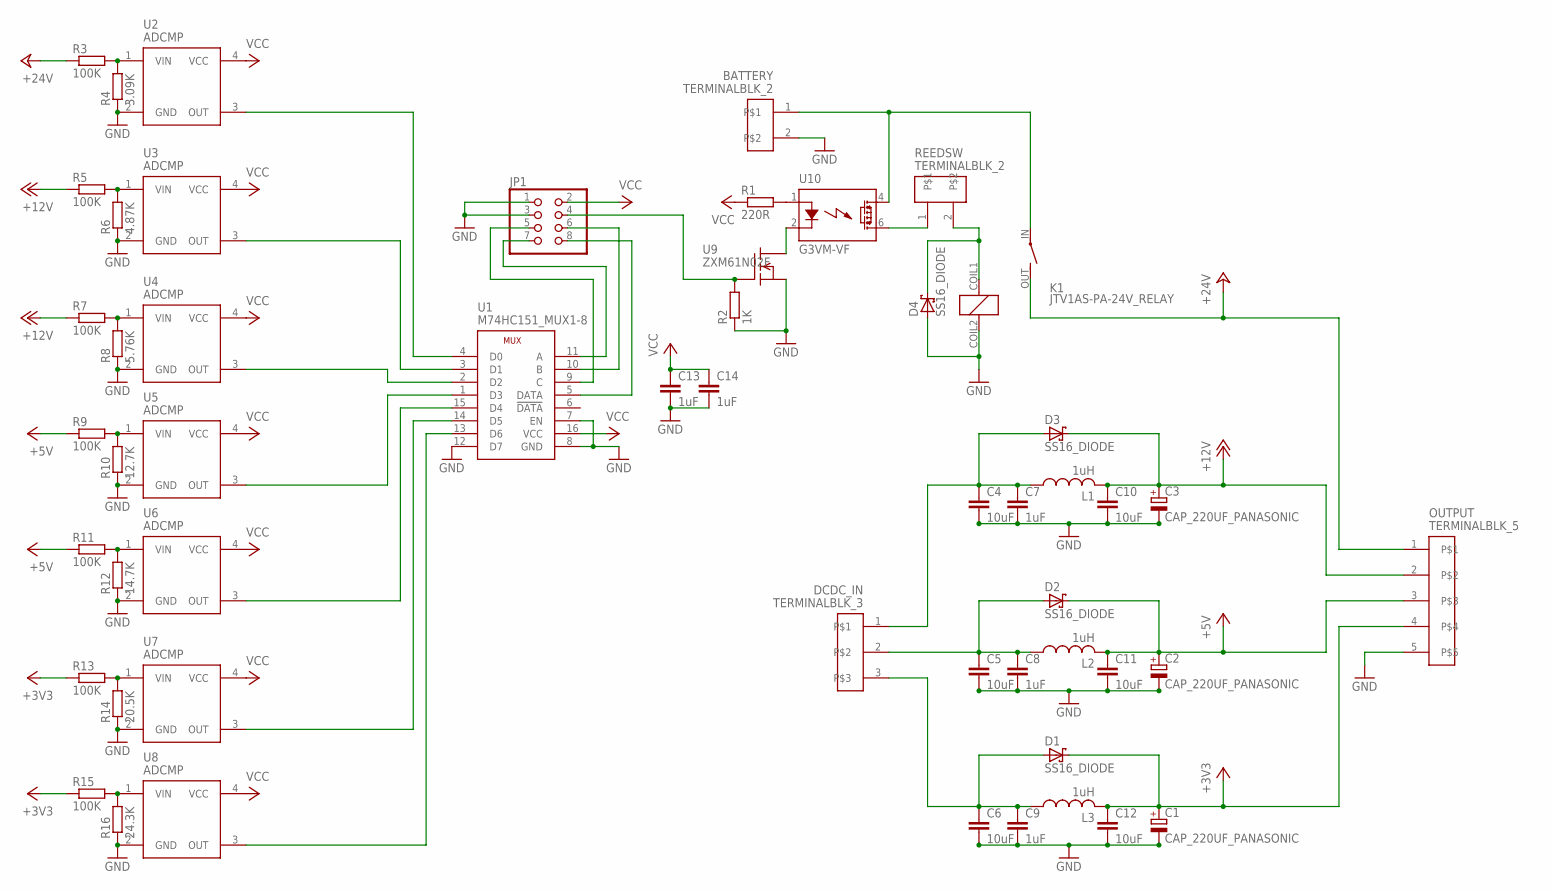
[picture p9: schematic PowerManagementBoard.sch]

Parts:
BATTERY: TERMINALBLK_2; TERMINAL_BLK-2
C1, C2, C3: CAP_220UF_PANASONIC
C4, C5, C6, C10, C11, C12: 10uF; C1206
C7, C8, C9, C13, C14: 1uF; C1206
D1, D2, D3, D4: SS16_DIODE; DO214AC
DCDC_IN: TERMINALBLK_3; TERMINAL_BLK-3
JP1: PINHD-2X4; 2X04
K1: JTV1AS-PA-24V_RELAY; JTV-RELAY_FORM1A
L1, L2, L3: 1uH; CHOKE_WE-HCC_8070
OUTPUT: TERMINALBLK_5; TERMINAL_BLK-5
R1: 220R; R0603
R2: 1K; R0603
R3, R5, R7, R9, R11, R13, R15: 100K; R0603
R4: 3.09K; R0603
R6: 4.87K; R0603
R8: 5.76K; R0603
R10: 12.7K; R0603
R12: 14.7K; R0603
R14: 20.5K; R0603
R16: 24.3K; R0603
REEDSW: TERMINALBLK_2; TERMINAL_BLK-2
U1: M74HC151_MUX1-8; TSSOP16
U2, U3, U4, U5, U6, U7, U8: ADCMP; SC70-4
U9: ZXM61N02F; SOT23W
U10: G3VM-VF

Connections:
+3V3: C1.P (+), C12.1, D1.C, L3.P$2 (2), OUTPUT.4, R13.1, R15.1
+5V: C2.P (+), C11.1, D2.C, L2.P$2 (2), OUTPUT.3, R9.1, R11.1
+12V: C3.P (+), C10.1, D3.C, L1.P$2 (2), OUTPUT.2, R5.1, R7.1
+24V: K1.OUT (S), OUTPUT.1, R3.1
GND: BATTERY.2, C1.N (-), C2.N (-), C3.N (-), C4.2, C5.2, C6.2, C7.2, C8.2, C9.2, C10.2, C11.2, C12.2, C13.2, C14.2, D4.A, JP1.1, JP1.3, K1.COIL2 (2), OUTPUT.5, R2.1, R4.1, R6.1, R8.1, R10.1, R12.1, R14.1, R16.1, U1.7 (EN), U1.8 (GND), U1.12 (D7), U2.2 (GND), U3.2 (GND), U4.2 (GND), U5.2 (GND), U6.2 (GND), U7.2 (GND), U8.2 (GND), U9.2 (S)
unnamed: BATTERY.1, K1.IN, U10.4 (DS1)
unnamed: REEDSW.1, U10.6 (DS2)
unnamed: D4.C, K1.COIL1 (1), REEDSW.2
unnamed: C6.1, C9.1, D1.A, DCDC_IN.3, L3.P$1 (1)
unnamed: C5.1, C8.1, D2.A, DCDC_IN.2, L2.P$1 (1)
unnamed: C4.1, C7.1, D3.A, DCDC_IN.1, L1.P$1 (1)
unnamed: U9.3 (D), U10.2 (K)
unnamed: R1.2, U10.1 (A)
unnamed: JP1.4, R2.2, U9.1 (G)
unnamed: JP1.8, U1.5 (DATA)
unnamed: JP1.6, U1.10 (B)
unnamed: JP1.7, U1.11 (A)
unnamed: JP1.5, U1.9 (C)
unnamed: R3.2, R4.2, U2.1 (VIN)
unnamed: R5.2, R6.2, U3.1 (VIN)
unnamed: R7.2, R8.2, U4.1 (VIN)
unnamed: R9.2, R10.2, U5.1 (VIN)
unnamed: R11.2, R12.2, U6.1 (VIN)
unnamed: R13.2, R14.2, U7.1 (VIN)
unnamed: R15.2, R16.2, U8.1 (VIN)
unnamed: U1.4 (D0), U2.3 (OUT)
unnamed: U1.3 (D1), U3.3 (OUT)
unnamed: U1.2 (D2), U4.3 (OUT)
unnamed: U1.1 (D3), U5.3 (OUT)
unnamed: U1.15 (D4), U6.3 (OUT)
unnamed: U1.14 (D5), U7.3 (OUT)
unnamed: U1.13 (D6), U8.3 (OUT)
VCC: C13.1, C14.1, JP1.2, R1.1, U1.16 (VCC), U2.4 (VCC), U3.4 (VCC), U4.4 (VCC), U5.4 (VCC), U6.4 (VCC), U7.4 (VCC), U8.4 (VCC)

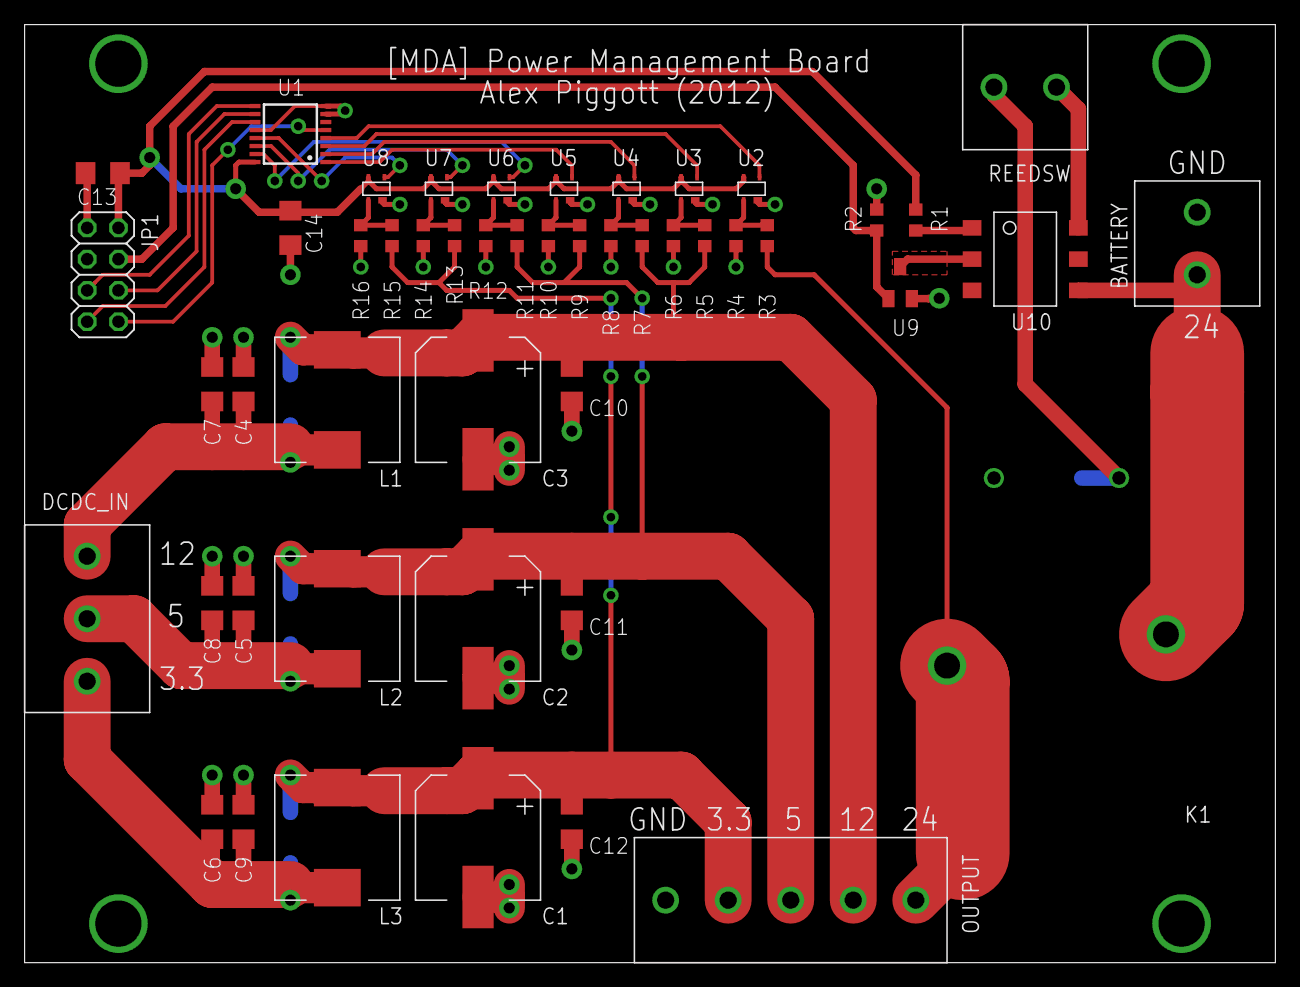
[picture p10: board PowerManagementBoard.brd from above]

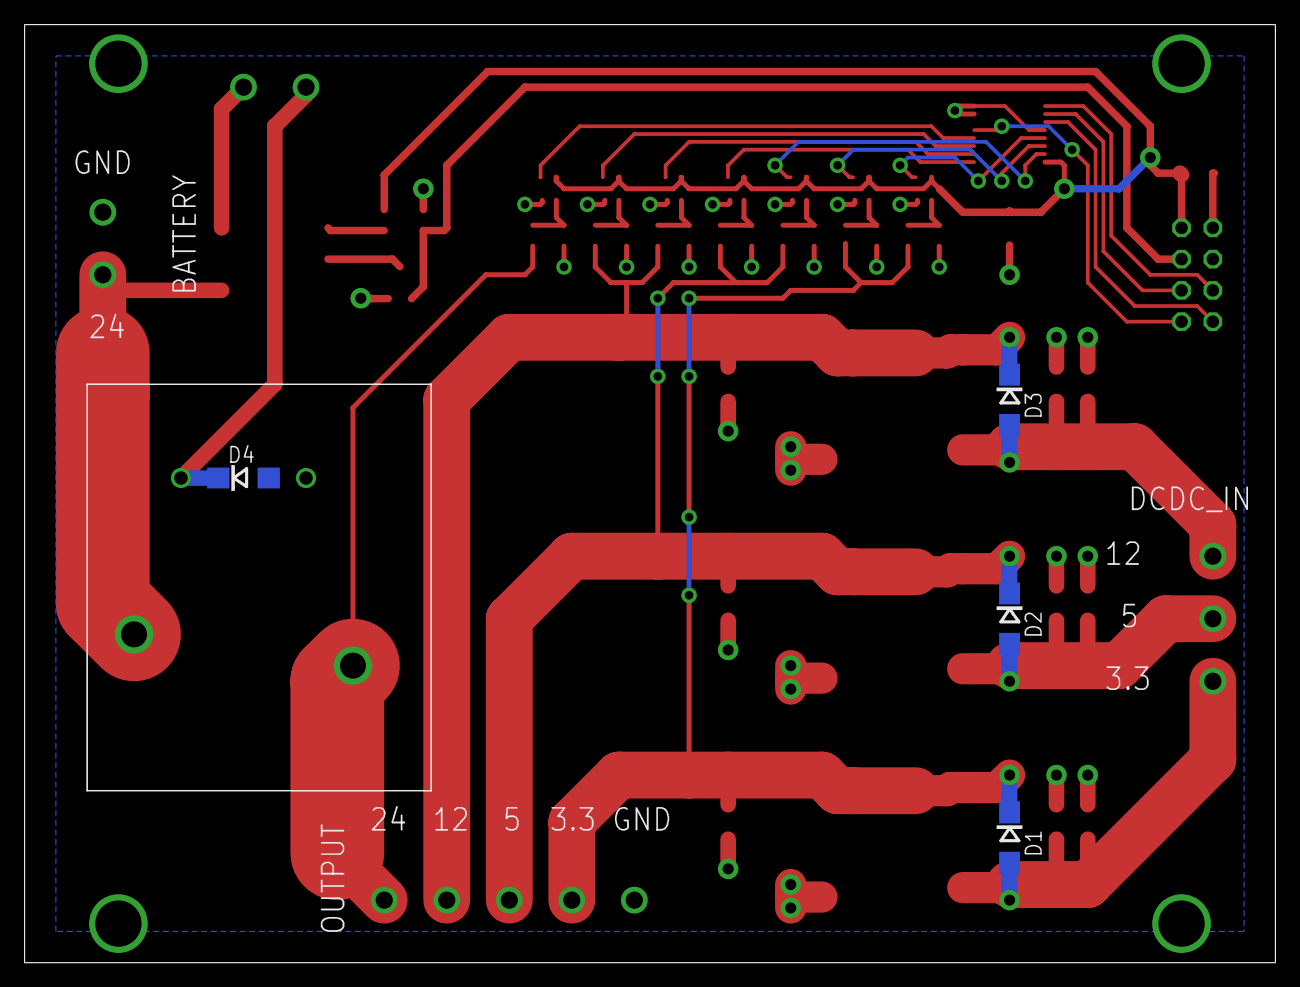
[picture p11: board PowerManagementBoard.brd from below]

Board: 2 copper layers, 101.6 x 76.2 mm, 53 parts (4 on the bottom side), 33 nets.

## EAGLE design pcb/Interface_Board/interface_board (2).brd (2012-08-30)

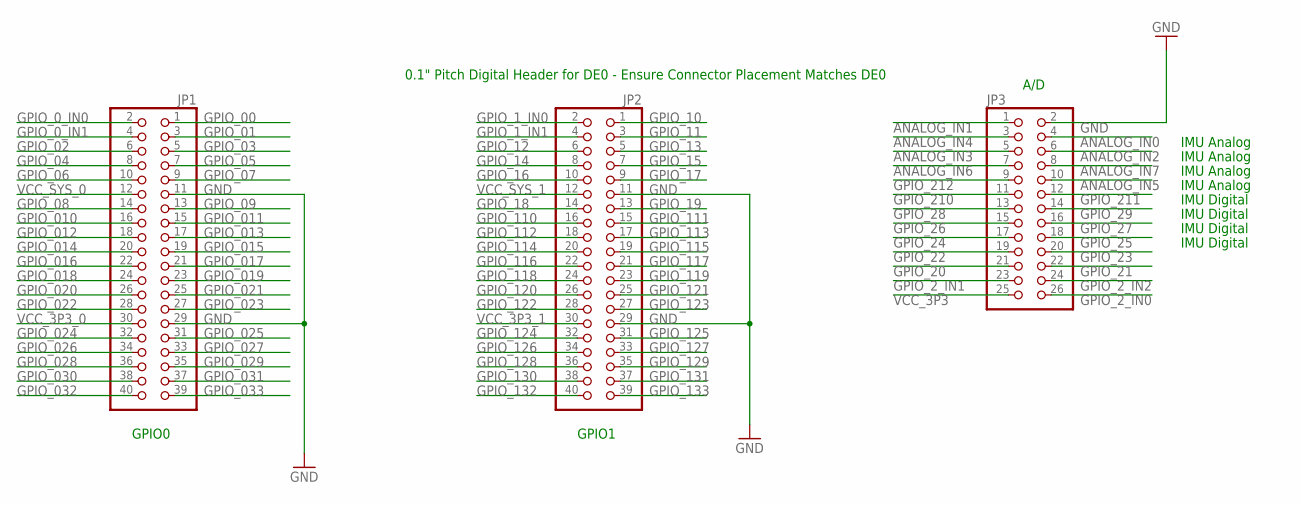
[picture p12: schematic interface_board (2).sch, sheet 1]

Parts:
JP1, JP2: PINHD-2X20; 2X20
JP3: PINHD-2X13; 2X13

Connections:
ANALOG_IN0: JP3.4; also elsewhere on the board
ANALOG_IN1: JP3.1; also elsewhere on the board
ANALOG_IN2: JP3.6; also elsewhere on the board
ANALOG_IN3: JP3.5; also elsewhere on the board
ANALOG_IN4: JP3.3; also elsewhere on the board
ANALOG_IN5: JP3.10; also elsewhere on the board
ANALOG_IN6: JP3.7; also elsewhere on the board
ANALOG_IN7: JP3.8; also elsewhere on the board
GND: JP1.11, JP1.29, JP2.11, JP2.29, JP3.2; also elsewhere on the board
GPIO_00: JP1.1; also elsewhere on the board
GPIO_0_IN0: JP1.2; also elsewhere on the board
GPIO_0_IN1: JP1.4; also elsewhere on the board
GPIO_01: JP1.3; also elsewhere on the board
GPIO_1_IN0: JP2.2; also elsewhere on the board
GPIO_1_IN1: JP2.4; also elsewhere on the board
GPIO_02: JP1.6; also elsewhere on the board
GPIO_2_IN0: JP3.26; also elsewhere on the board
GPIO_2_IN1: JP3.23; also elsewhere on the board
GPIO_2_IN2: JP3.24; also elsewhere on the board
GPIO_03: JP1.5; also elsewhere on the board
GPIO_04: JP1.8; also elsewhere on the board
GPIO_05: JP1.7; also elsewhere on the board
GPIO_06: JP1.10; also elsewhere on the board
GPIO_07: JP1.9; also elsewhere on the board
GPIO_08: JP1.14; also elsewhere on the board
GPIO_09: JP1.13; also elsewhere on the board
GPIO_010: JP1.16; also elsewhere on the board
GPIO_10: JP2.1; also elsewhere on the board
GPIO_011: JP1.15; also elsewhere on the board
GPIO_11: JP2.3; also elsewhere on the board
GPIO_012: JP1.18; also elsewhere on the board
GPIO_12: JP2.6; also elsewhere on the board
GPIO_013: JP1.17; also elsewhere on the board
GPIO_13: JP2.5; also elsewhere on the board
GPIO_014: JP1.20; also elsewhere on the board
GPIO_14: JP2.8; also elsewhere on the board
GPIO_015: JP1.19; also elsewhere on the board
GPIO_15: JP2.7; also elsewhere on the board
GPIO_016: JP1.22; also elsewhere on the board
GPIO_16: JP2.10; also elsewhere on the board
GPIO_017: JP1.21; also elsewhere on the board
GPIO_17: JP2.9; also elsewhere on the board
GPIO_018: JP1.24; also elsewhere on the board
GPIO_18: JP2.14; also elsewhere on the board
GPIO_019: JP1.23; also elsewhere on the board
GPIO_19: JP2.13; also elsewhere on the board
GPIO_020: JP1.26; also elsewhere on the board
GPIO_20: JP3.21; also elsewhere on the board
GPIO_021: JP1.25; also elsewhere on the board
GPIO_21: JP3.22; also elsewhere on the board
GPIO_022: JP1.28; also elsewhere on the board
GPIO_22: JP3.19; also elsewhere on the board
GPIO_023: JP1.27; also elsewhere on the board
GPIO_23: JP3.20; also elsewhere on the board
GPIO_024: JP1.32; also elsewhere on the board
GPIO_24: JP3.17; also elsewhere on the board
GPIO_025: JP1.31; also elsewhere on the board
GPIO_25: JP3.18; also elsewhere on the board
GPIO_026: JP1.34; also elsewhere on the board
GPIO_26: JP3.15; also elsewhere on the board
GPIO_027: JP1.33; also elsewhere on the board
GPIO_27: JP3.16; also elsewhere on the board
GPIO_028: JP1.36; also elsewhere on the board
GPIO_28: JP3.13; also elsewhere on the board
GPIO_029: JP1.35; also elsewhere on the board
GPIO_29: JP3.14; also elsewhere on the board
GPIO_030: JP1.38; also elsewhere on the board
GPIO_031: JP1.37; also elsewhere on the board
GPIO_032: JP1.40; also elsewhere on the board
GPIO_033: JP1.39; also elsewhere on the board
GPIO_110: JP2.16; also elsewhere on the board
GPIO_111: JP2.15; also elsewhere on the board
GPIO_112: JP2.18; also elsewhere on the board
GPIO_113: JP2.17; also elsewhere on the board
GPIO_114: JP2.20; also elsewhere on the board
GPIO_115: JP2.19; also elsewhere on the board
GPIO_116: JP2.22; also elsewhere on the board
GPIO_117: JP2.21; also elsewhere on the board
GPIO_118: JP2.24; also elsewhere on the board
GPIO_119: JP2.23; also elsewhere on the board
GPIO_120: JP2.26; also elsewhere on the board
GPIO_121: JP2.25; also elsewhere on the board
GPIO_122: JP2.28; also elsewhere on the board
GPIO_123: JP2.27; also elsewhere on the board
GPIO_124: JP2.32; also elsewhere on the board
GPIO_125: JP2.31; also elsewhere on the board
GPIO_126: JP2.34; also elsewhere on the board
GPIO_127: JP2.33; also elsewhere on the board
GPIO_128: JP2.36; also elsewhere on the board
GPIO_129: JP2.35; also elsewhere on the board
GPIO_130: JP2.38; also elsewhere on the board
GPIO_131: JP2.37; also elsewhere on the board
GPIO_132: JP2.40; also elsewhere on the board
GPIO_133: JP2.39; also elsewhere on the board
GPIO_210: JP3.11; also elsewhere on the board
GPIO_211: JP3.12; also elsewhere on the board
GPIO_212: JP3.9; also elsewhere on the board
VCC_3P3: JP3.25; also elsewhere on the board
VCC_3P3_0: JP1.30
VCC_3P3_1: JP2.30; also elsewhere on the board
VCC_SYS_0: JP1.12
VCC_SYS_1: JP2.12

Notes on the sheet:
0.1" Pitch Digital Header for DE0 - Ensure Connector Placement Matches DE0
GPIO0
GPIO1
A/D
IMU Analog
IMU Digital

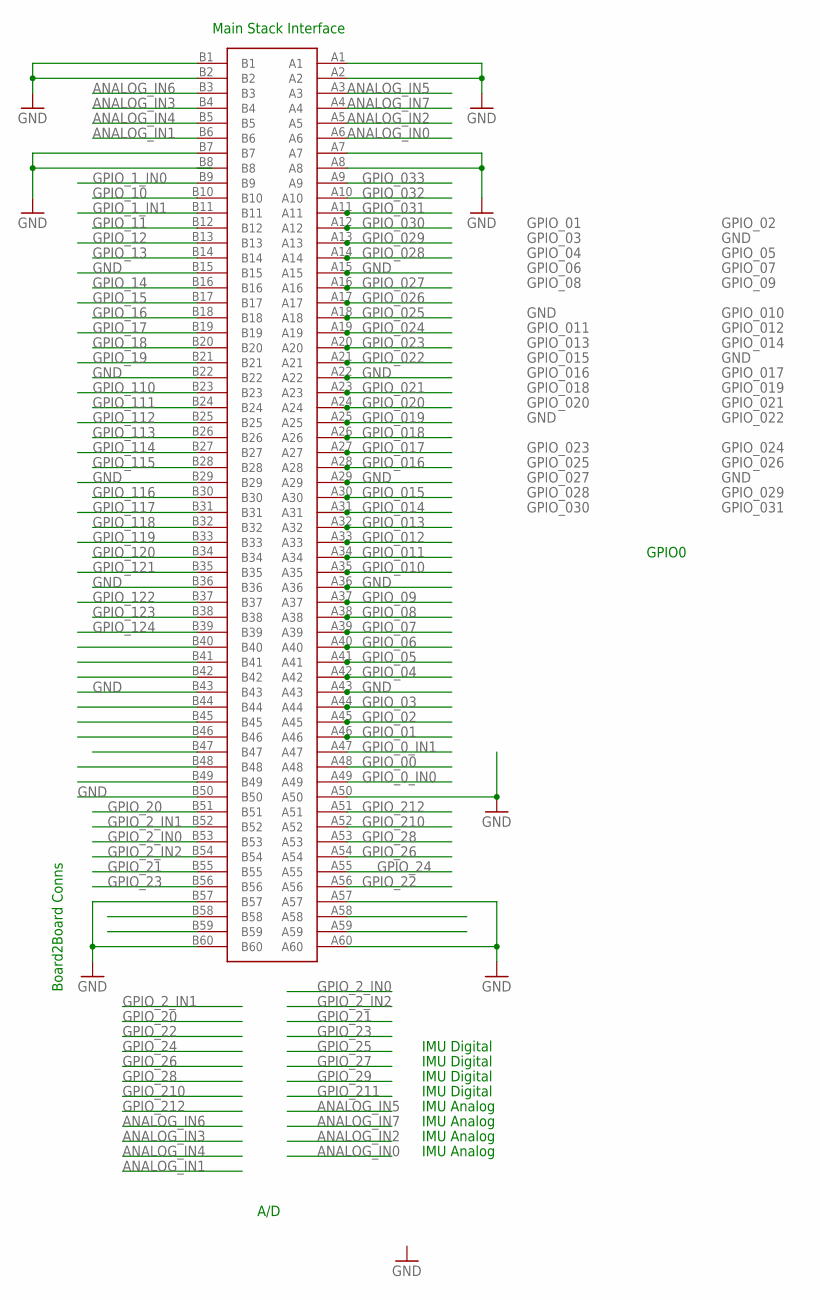
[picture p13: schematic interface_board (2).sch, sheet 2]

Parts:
U$10: MAIN-STACK-CONN-WIDEPITCH; STACK-CONN-WIDEPITCH

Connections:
ANALOG_IN0: U$10.A6; also elsewhere on the board
ANALOG_IN1: U$10.B6; also elsewhere on the board
ANALOG_IN2: U$10.A5; also elsewhere on the board
ANALOG_IN3: U$10.B4; also elsewhere on the board
ANALOG_IN4: U$10.B5; also elsewhere on the board
ANALOG_IN5: U$10.A3; also elsewhere on the board
ANALOG_IN6: U$10.B3; also elsewhere on the board
ANALOG_IN7: U$10.A4; also elsewhere on the board
GND: U$10.A1, U$10.A2, U$10.A7, U$10.A8, U$10.A15, U$10.A22, U$10.A29, U$10.A36, U$10.A43, U$10.A50, U$10.A57, U$10.A60, U$10.B1, U$10.B2, U$10.B7, U$10.B15, U$10.B22, U$10.B29, U$10.B36, U$10.B43, U$10.B50, U$10.B57, U$10.B60; also elsewhere on the board
GPIO_00: U$10.A48; also elsewhere on the board
GPIO_0_IN0: U$10.A49; also elsewhere on the board
GPIO_0_IN1: U$10.A47; also elsewhere on the board
GPIO_01: U$10.A46; also elsewhere on the board
GPIO_1_IN0: U$10.B9; also elsewhere on the board
GPIO_1_IN1: U$10.B11; also elsewhere on the board
GPIO_02: U$10.A45; also elsewhere on the board
GPIO_2_IN0: U$10.B53; also elsewhere on the board
GPIO_2_IN1: U$10.B52; also elsewhere on the board
GPIO_2_IN2: U$10.B54; also elsewhere on the board
GPIO_03: U$10.A44; also elsewhere on the board
GPIO_04: U$10.A42; also elsewhere on the board
GPIO_05: U$10.A41; also elsewhere on the board
GPIO_06: U$10.A40; also elsewhere on the board
GPIO_07: U$10.A39; also elsewhere on the board
GPIO_08: U$10.A38; also elsewhere on the board
GPIO_09: U$10.A37; also elsewhere on the board
GPIO_010: U$10.A35; also elsewhere on the board
GPIO_10: U$10.B10; also elsewhere on the board
GPIO_011: U$10.A34; also elsewhere on the board
GPIO_11: U$10.B12; also elsewhere on the board
GPIO_012: U$10.A33; also elsewhere on the board
GPIO_12: U$10.B13; also elsewhere on the board
GPIO_013: U$10.A32; also elsewhere on the board
GPIO_13: U$10.B14; also elsewhere on the board
GPIO_014: U$10.A31; also elsewhere on the board
GPIO_14: U$10.B16; also elsewhere on the board
GPIO_015: U$10.A30; also elsewhere on the board
GPIO_15: U$10.B17; also elsewhere on the board
GPIO_016: U$10.A28; also elsewhere on the board
GPIO_16: U$10.B18; also elsewhere on the board
GPIO_017: U$10.A27; also elsewhere on the board
GPIO_17: U$10.B19; also elsewhere on the board
GPIO_018: U$10.A26; also elsewhere on the board
GPIO_18: U$10.B20; also elsewhere on the board
GPIO_019: U$10.A25; also elsewhere on the board
GPIO_19: U$10.B21; also elsewhere on the board
GPIO_020: U$10.A24; also elsewhere on the board
GPIO_20: U$10.B51; also elsewhere on the board
GPIO_021: U$10.A23; also elsewhere on the board
GPIO_21: U$10.B55; also elsewhere on the board
GPIO_022: U$10.A21; also elsewhere on the board
GPIO_22: U$10.A56; also elsewhere on the board
GPIO_023: U$10.A20; also elsewhere on the board
GPIO_23: U$10.B56; also elsewhere on the board
GPIO_024: U$10.A19; also elsewhere on the board
GPIO_24: U$10.A55; also elsewhere on the board
GPIO_025: U$10.A18; also elsewhere on the board
GPIO_026: U$10.A17; also elsewhere on the board
GPIO_26: U$10.A54; also elsewhere on the board
GPIO_027: U$10.A16; also elsewhere on the board
GPIO_028: U$10.A14; also elsewhere on the board
GPIO_28: U$10.A53; also elsewhere on the board
GPIO_029: U$10.A13; also elsewhere on the board
GPIO_030: U$10.A12; also elsewhere on the board
GPIO_031: U$10.A11; also elsewhere on the board
GPIO_032: U$10.A10; also elsewhere on the board
GPIO_033: U$10.A9; also elsewhere on the board
GPIO_110: U$10.B23; also elsewhere on the board
GPIO_111: U$10.B24; also elsewhere on the board
GPIO_112: U$10.B25; also elsewhere on the board
GPIO_113: U$10.B26; also elsewhere on the board
GPIO_114: U$10.B27; also elsewhere on the board
GPIO_115: U$10.B28; also elsewhere on the board
GPIO_116: U$10.B30; also elsewhere on the board
GPIO_117: U$10.B31; also elsewhere on the board
GPIO_118: U$10.B32; also elsewhere on the board
GPIO_119: U$10.B33; also elsewhere on the board
GPIO_120: U$10.B34; also elsewhere on the board
GPIO_121: U$10.B35; also elsewhere on the board
GPIO_122: U$10.B37; also elsewhere on the board
GPIO_123: U$10.B38; also elsewhere on the board
GPIO_124: U$10.B39; also elsewhere on the board
GPIO_210: U$10.A52; also elsewhere on the board
GPIO_212: U$10.A51; also elsewhere on the board

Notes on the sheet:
Main Stack Interface
GPIO0
A/D
IMU Analog
IMU Digital
Board2Board Conns

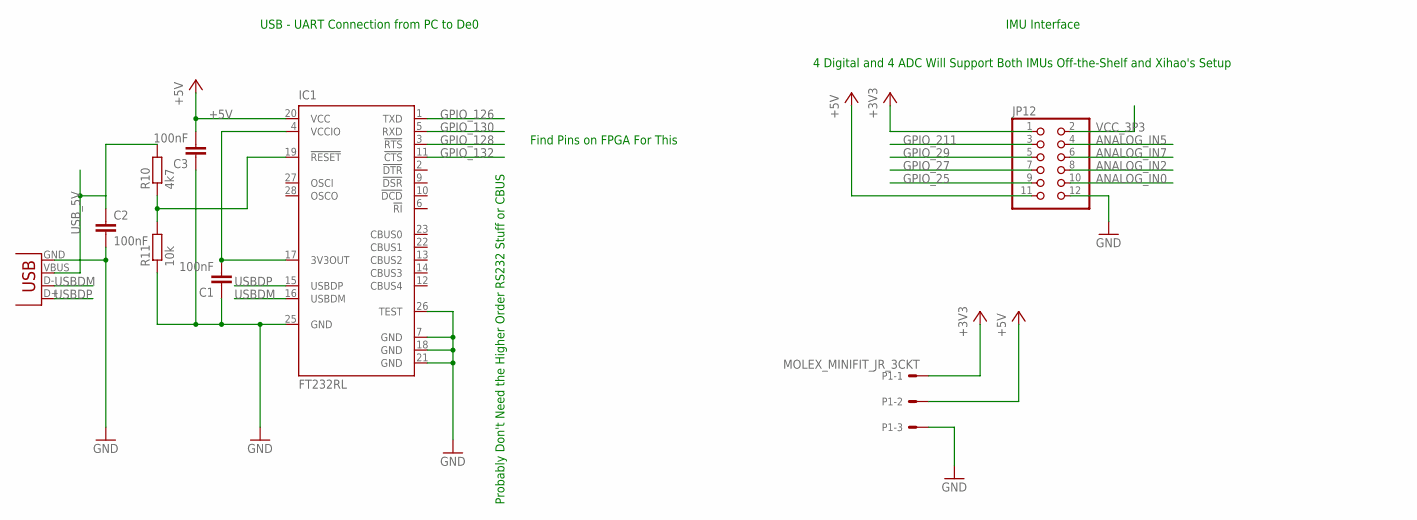
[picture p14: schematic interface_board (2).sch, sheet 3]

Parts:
C1, C2, C3: 100nF; C0805
IC1: FT232RL; SSOP28
JP12: PINHD-2X6; 2X06
P1: MOLEX_MINIFIT_JR_3CKT; 3CKT_MINIFIT_JR
R10: 4k7; M0805
R11: 10k; M0805
X1: USBSMD; USB-MINIB

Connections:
+3V3: JP12.1, P1.1; also elsewhere on the board
+5V: C3.2, IC1.20 (VCC), JP12.11, P1.2
ANALOG_IN0: JP12.10; also elsewhere on the board
ANALOG_IN2: JP12.8; also elsewhere on the board
ANALOG_IN5: JP12.4; also elsewhere on the board
ANALOG_IN7: JP12.6; also elsewhere on the board
GND: C1.1, C2.2, C3.1, IC1.7 (GND), IC1.18 (GND), IC1.21 (GND), IC1.25 (GND), IC1.26 (TEST), JP12.12, P1.3, R11.1, X1.GND; also elsewhere on the board
GPIO_25: JP12.9; also elsewhere on the board
GPIO_27: JP12.7; also elsewhere on the board
GPIO_29: JP12.5; also elsewhere on the board
GPIO_126: IC1.1 (TXD); also elsewhere on the board
GPIO_128: IC1.3 (!RTS); also elsewhere on the board
GPIO_130: IC1.5 (RXD); also elsewhere on the board
GPIO_132: IC1.11 (!CTS); also elsewhere on the board
GPIO_211: JP12.3; also elsewhere on the board
unnamed: C1.2, IC1.4 (VCCIO), IC1.17 (3V3OUT)
unnamed: IC1.19 (!RESET), R10.1, R11.2
USBDM: IC1.16 (USBDM), X1.D-
USBDP: IC1.15 (USBDP), X1.D+
USB_5V: C2.1, R10.2, X1.VBUS
VCC_3P3: JP12.2; also elsewhere on the board

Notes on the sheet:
USB - UART Connection from PC to De0
IMU Interface
Probably Don't Need the Higher Order RS232 Stuff or CBUS
Find Pins on FPGA For This
4 Digital and 4 ADC Will Support Both IMUs Off-the-Shelf and Xihao's Setup

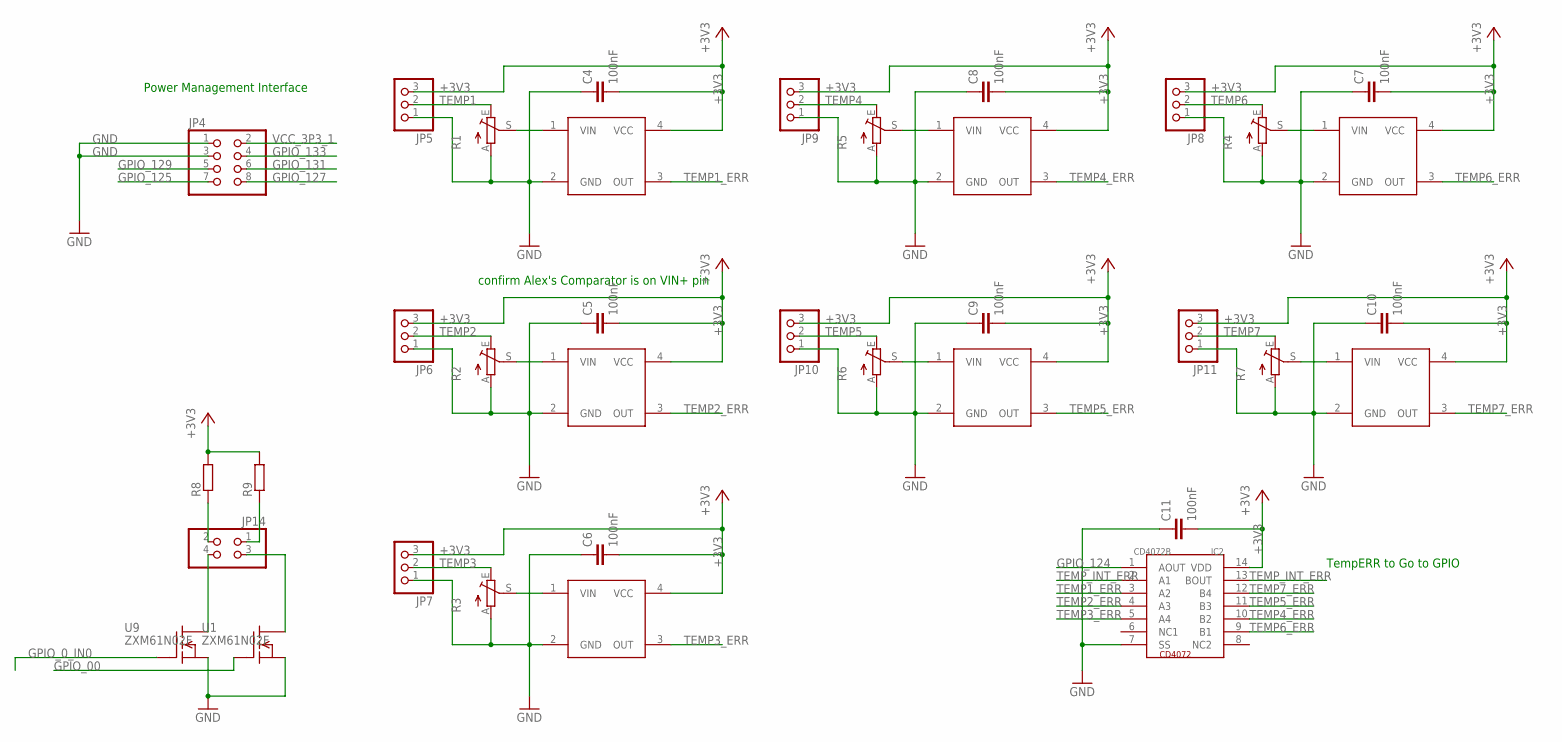
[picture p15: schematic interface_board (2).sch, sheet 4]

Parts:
C4, C5, C6, C7, C8, C9, C10, C11: 100nF; C0805
IC2: CD4072B; SO14
JP4: PINHD-2X4; 2X04
JP5, JP6, JP7, JP8, JP9, JP10, JP11: PINHD-1X3; 1X03
JP14: PINHD-2X2; 2X02
R1, R2, R3, R4, R5, R6, R7: TRIM_1234-S64YW; POT
R8, R9: R-EU_M1206; M1206
U1, U9: ZXM61N02F; SOT23W
U$2, U$4, U$5, U$6, U$7, U$8, U$9: ADCMP

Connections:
+3V3: C4.2, C5.2, C6.2, C7.2, C8.2, C9.2, C10.2, C11.2, IC2.14 (VDD), JP5.3, JP6.3, JP7.3, JP8.3, JP9.3, JP10.3, JP11.3, R8.2, R9.2, U$2.4 (VCC), U$4.4 (VCC), U$5.4 (VCC), U$6.4 (VCC), U$7.4 (VCC), U$8.4 (VCC), U$9.4 (VCC); also elsewhere on the board
GND: C4.1, C5.1, C6.1, C7.1, C8.1, C9.1, C10.1, C11.1, IC2.7 (SS), JP4.1, JP4.3, JP5.1, JP6.1, JP7.1, JP8.1, JP9.1, JP10.1, JP11.1, R1.A, R2.A, R3.A, R4.A, R5.A, R6.A, R7.A, U1.2 (S), U9.2 (S), U$2.2 (GND), U$4.2 (GND), U$5.2 (GND), U$6.2 (GND), U$7.2 (GND), U$8.2 (GND), U$9.2 (GND); also elsewhere on the board
GPIO_00: U1.1 (G); also elsewhere on the board
GPIO_0_IN0: U9.1 (G); also elsewhere on the board
GPIO_124: IC2.1 (AOUT); also elsewhere on the board
GPIO_125: JP4.7; also elsewhere on the board
GPIO_127: JP4.8; also elsewhere on the board
GPIO_129: JP4.5; also elsewhere on the board
GPIO_131: JP4.6; also elsewhere on the board
GPIO_133: JP4.4; also elsewhere on the board
unnamed: R1.S, U$2.1 (VIN)
unnamed: R2.S, U$4.1 (VIN)
unnamed: R3.S, U$5.1 (VIN)
unnamed: R4.S, U$6.1 (VIN)
unnamed: R5.S, U$7.1 (VIN)
unnamed: R6.S, U$8.1 (VIN)
unnamed: R7.S, U$9.1 (VIN)
unnamed: JP14.2, R8.1
unnamed: JP14.4, U9.3 (D)
unnamed: JP14.1, R9.1
unnamed: JP14.3, U1.3 (D)
TEMP1: JP5.2, R1.E
TEMP1_ERR: IC2.3 (A2), U$2.3 (OUT)
TEMP2: JP6.2, R2.E
TEMP2_ERR: IC2.4 (A3), U$4.3 (OUT)
TEMP3: JP7.2, R3.E
TEMP3_ERR: IC2.5 (A4), U$5.3 (OUT)
TEMP4: JP9.2, R5.E
TEMP4_ERR: IC2.10 (B2), U$7.3 (OUT)
TEMP5: JP10.2, R6.E
TEMP5_ERR: IC2.11 (B3), U$8.3 (OUT)
TEMP6: JP8.2, R4.E
TEMP6_ERR: IC2.9 (B1), U$6.3 (OUT)
TEMP7: JP11.2, R7.E
TEMP7_ERR: IC2.12 (B4), U$9.3 (OUT)
TEMP_INT_ERR: IC2.2 (A1), IC2.13 (BOUT)
VCC_3P3_1: JP4.2; also elsewhere on the board

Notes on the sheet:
Power Management Interface
TempERR to Go to GPIO
confirm Alex's Comparator is on VIN+ pin

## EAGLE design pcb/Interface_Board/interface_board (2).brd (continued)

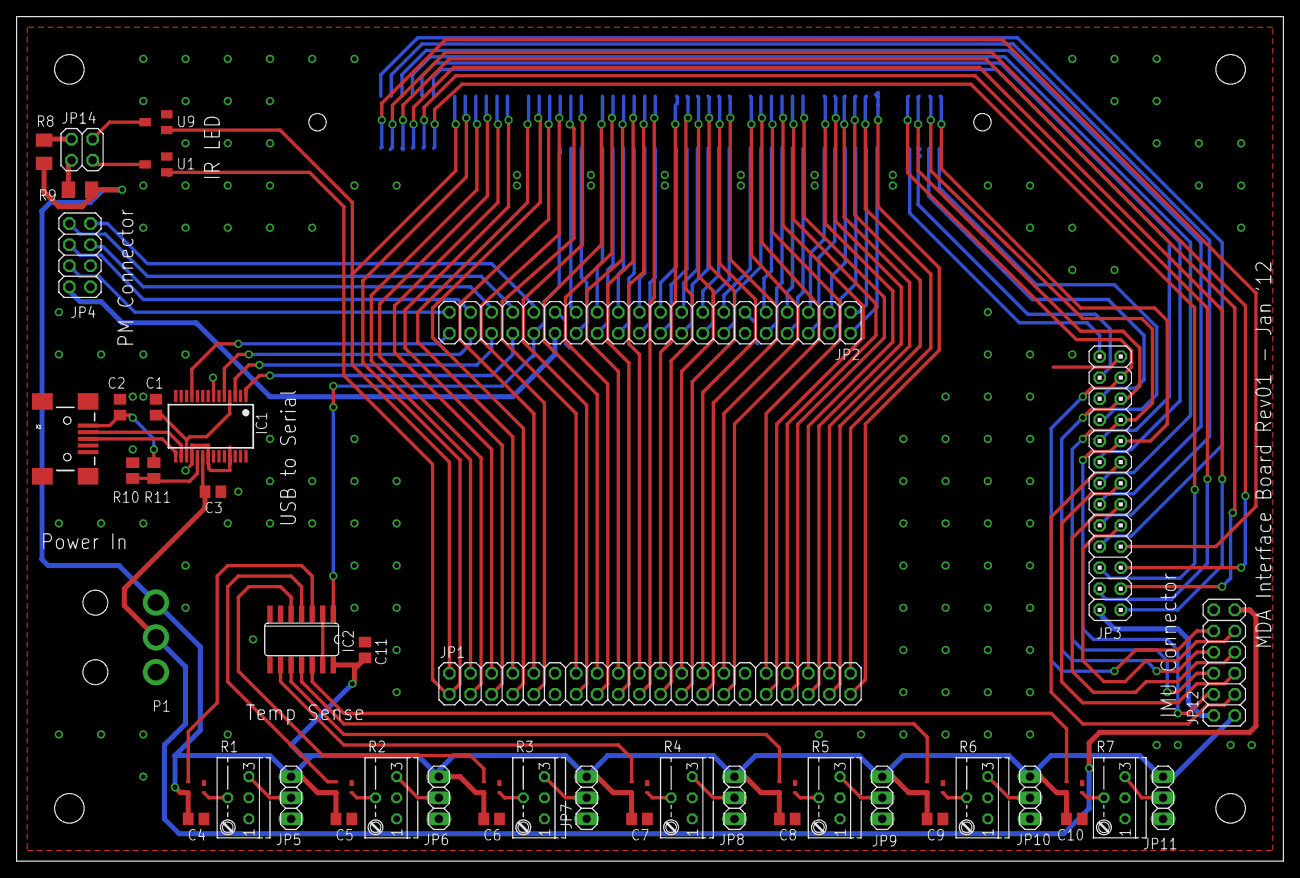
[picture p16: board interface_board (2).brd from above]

Board: 2 copper layers, 152.4 x 101.6 mm, 49 parts (1 on the bottom side), 132 nets.

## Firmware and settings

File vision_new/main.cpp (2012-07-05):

/** The main function is just used to test various parts of vision. Rewrite
 *  as needed 
 */
#include <stdlib.h>
#include <stdio.h>

#include "lib/mv.h"
#include "lib/mgui.h"

int main () {
    char filename[] = "settings/settings.msf";
    float S1, S2;
    
    read_mv_setting (filename, "S1", S1);
    read_mv_setting (filename, "S2", S2);
    
    printf ("S1: %f\nS2: %f\n", S1, S2);
                      
    return 0;
}

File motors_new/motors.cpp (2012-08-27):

#include "motors.h"
#include <math.h>

void Motors::move(MOVE_DIR dir, float accel)
{
   switch(dir) {
   case FORWARD:
      model->accel += accel*FWD_ACCEL_CONST;
      break;
   case REVERSE:
      model->accel -= accel*FWD_ACCEL_CONST;
      break;
   case RISE:
      model->depth_accel += accel*DEPTH_ACCEL_CONST;
      break;
   case SINK:
      model->depth_accel -= accel*DEPTH_ACCEL_CONST;
      break;
   case RIGHT:
      model->angular_accel += accel*ANG_ACCEL_CONST;
      break;
   case LEFT:
      model->angular_accel -= accel*ANG_ACCEL_CONST;
      break;
   case STOP:
      model->accel = 0;
      model->depth_accel = 0;
      model->angular_accel = 0;
      break;
   }
}

void Motors::translate(MOVE_DIR dir)
{
    switch(dir) {
        case FORWARD:
            model->position.z -= POS_INC*cos((model->angle.yaw*PI)/180)*cos((model->angle.pitch*PI)/180);
            model->position.x += POS_INC*sin((model->angle.yaw*PI)/180)*cos((model->angle.pitch*PI)/180);
            model->position.y -= POS_INC*sin((model->angle.pitch*PI)/180);
            break;
        case REVERSE:
            model->position.z += POS_INC*cos((model->angle.yaw*PI)/180)*cos((model->angle.pitch*PI)/180);
            model->position.x -= POS_INC*sin((model->angle.yaw*PI)/180)*cos((model->angle.pitch*PI)/180);
            model->position.y += POS_INC*sin((model->angle.pitch*PI)/180);
            break;
        case RISE:
            model->position.y += POS_INC;
            break;
        case SINK:
            model->position.y -= POS_INC;
            break;
        case RIGHT:
            model->angle.yaw += ANGLE_INC/2;
            break;
        case LEFT:
            model->angle.yaw -= ANGLE_INC/2;
            break;
        case STOP:
            model->speed = 0;
            model->depth_speed = 0;
            model->angular_speed = 0;
            break;
    }
}

void Motors::key_command (char key) {
    switch (key) {
        case '0': // set speed from 0-9
        case '1':
        case '2':
        case '3':
        case '4':
        case '5':
        case '6':
        case '7':
        case '8':
        case '9':
            move (FORWARD, (int)(key - '0'));
            break;
        case 'w':
            move (FORWARD);
            break;
        case 's':
            move (REVERSE);
            break;
        case 'a':
            move (LEFT);
            break;
        case 'd':
            move (RIGHT);
            break;
        case 'r':
            move (RISE);
            break;
        case 'f':
            move (SINK);
            break;
        // translations
        case 'i': // forwards/back and turn is wasd
            translate(FORWARD);
            break;
        case 'k':
            translate(REVERSE);
            break;
        case 'j':
            translate(LEFT);
            break;
        case 'l':
            translate(RIGHT);
            break;
        case 'o':
            translate(RISE);
            break;
        case ';':
            translate(SINK);
            break;
        case '.':
        case ' ':
            move(STOP);
            break;
        default:
            model->accel = 0;
            model->depth_accel = 0;
            model->angular_accel = 0;
            break;
    }
}

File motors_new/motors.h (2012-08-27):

#ifndef MOTORS_H
#define MOTORS_H

#include "../sim_new/physical_model.h"
#include <stdlib.h>

#define DEFAULT_ACCEL 1
#define FWD_ACCEL_CONST 0.02
#define DEPTH_ACCEL_CONST 0.06
#define ANG_ACCEL_CONST 0.1

enum MOVE_DIR {
  STOP,
  FORWARD,
  REVERSE,
  LEFT,
  RIGHT,
  SINK,
  RISE
};

enum DEBUG_CMD {
  SCREENSHOT,
  RESET_POS,
  RESET_ALL,
  CMD_EXIT
};

class Motors {
  public:
    Motors (physical_model *m = NULL) : model(m) {}
    
    // code interface
    void move(MOVE_DIR dir, float accel);
    void move(MOVE_DIR dir) { move(dir, DEFAULT_ACCEL); }
    
    // keyboard interface
    void key_command (char key);

    // Only for the simulator
    void translate(MOVE_DIR dir);
    void debug(DEBUG_CMD cmd);
    
  private:
    physical_model *model; // this deals with velocities in the sim
};

#endif

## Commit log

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2011-06-06 added a project for the DE2
    To Compile:
    1. Open this the Quartus project with Quartus
    2. Open the SOPC builder
    3. Generate the SOPC
    4. Close the SPOC builder
    5. Compile the verilog
    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
    [DE2_pin_assignments.csv]
2011-06-06 Ok it should work, but the processor now goes in an infinite exception loop.
    I'll try to fix this tomorrow
    Everything should compile if you just type "make" on the top level module
    given that you are in a nios2_command_shell
    make sure you follow the instructions on the wiki to get it all going
    [main.c]
2011-06-06 wow it works now,
    not only do you have to specify the directory, but you need to specify the elf file, it won't automatically take one
    [main.c]
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2011-06-07 fixed the lcd.
    I just had to turn it on. THere is a pin "LCD_ON" that you have to set high.
    I also set the "LCD_BLON" high at the same time. I figured I might as well
    [main.c]
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2011-06-11 Moving a bunch of stuff around just to create organization in the folders
    Each folder will have a README.txt that people should read before adding code
    [DE2_pin_assignments.csv]
2011-06-11 Alright, it makes the navigation board
    still nead to "clean" the bsp directory
    [DE2_pin_assignments.csv]
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2011-06-25 Fixes to motor_controller. Added motor_controller to SOPC and connected GPIO_0[23:0] to the motor_controller.
    Created a Quartus project to demonstrate the motor controller's pwm.
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2011-07-18 Fixing bugs so that it works on the board.
    [main.c]
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2011-08-07 Fixing 'h' command to print out all descriptions.
    [main.c]
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2011-08-21 Fixed errors from last commit (tested on board).
2011-08-21 Fixing use of pwm defines. Tested working on board with different frequencies and a cycling duty cycle (0-80%).
2011-08-21 Implemented (and tested on board and simulation) anti-phase waveform to charge boost cap on motor circuit. This waveform drives in reverse when it is not driving forward.
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2011-09-24 Removed compile warnings and fixed includes.
    [cv_tasks.h, main.cpp]
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2011-10-29 Fixing fpga SW code so that set PWM frequency works as expected. It also keeps the same duty cycle.
    [main.c, utils.c]
2011-10-29 Fixing offset of 1 (oops).
    [main.c]
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2011-10-30 Clean up and fixing a printf statement in NIOS code.
    [main.c]
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2011-11-12 changed small things, readied code for sat tutorial nov 13 added range estimate using height corrected morphology. should be open followed by close
    [cv_tasks.h, main.cpp]
2011-11-12 Changing GPIO for motor driver output and fixing help on NIOS code.
    [main.c]
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2011-11-23 The sim now supports up/down, forward/reverse speed and positive/negative angular speed.
    [main.cpp]
2011-11-25 added bottom camera. Now images from both cams are retrieved and displayed. Also fixed some mem leaks.
    [main.cpp]
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2012-02-04 tested buoy task. Works. Corrected 0-180 wraparound mistakes in HSV. Wrote basic vers of pipe controller with no output.
    [main.cpp]
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2012-02-11 corrected segfault when running sim with task_*. removed extra variables in sim. Tried to test gate controller but img2 from downcam seems not to be passed to the controller properly.
    [main.cpp]
2012-02-11 corrected variable init bugs in sim, image orientation bugs in HSV_filter TAN_ANGLE may be wrong in task_PATH task_PATH controller has bugs, keep going to error state
    [main.cpp]
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2012-02-21 Finished task_U, but need to test. Have to change sim to put in the physical obstable. We can make changes to the barbed wire thing they have. Found a bug where pressing W in sim doesnt move foward, 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
    [main.cpp]
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2012-02-23 Began testing task_buoy. encountered difficulties due to the small size of the buoy in the actual image. Wrote vision_buoy2, which tries to use Hu moment matching to identify the circular-ness of an 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
    [main.cpp]
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2012-02-25 fixed movement bugs changed path controller a bit fixed sim makefile
    [main.cpp]
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2012-03-10 Fixed colors and sizes of objects in sim. Also fixed sizes in task_X.h Tested U vision function. Works fine. Found minor bug in task_path where if you are too far away the two lines for the pipe gets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
    [main.cpp]
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2012-03-17 Improved power management to connect to software through SOPC. Power management triggers an interrupt if there is an issue with the voltage levels.
    [main.c, utils.c]
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2012-05-16 Made power management code more flexible rather than failing on the first instance, it will count up to 100 and report all power failures.
    [main.c]
2012-05-19 - Wrote simple PI controller. It exponentially decays the integral term - Added the PI controller to all the control functions - path controller is buggy because vision cant handle single line... - o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
    [main.cpp]
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2012-06-02 Improve the interface on FPGA SW code. stop command works as expected and there's an 'all' command to set motor values.
    Add a hack to ignore 5-V failures because the board is faulty.
    [main.c]
2012-06-02 Fix top-level Makefile for motors.
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2012-06-27 A bit more code cleanup. Accelerometer still doesn't work though...
    [main.c]
2012-06-27 Remove hack since the 5V board has been fixed.
    [main.c]
2012-06-29 Cleaned up fpga_sw code slightly. Did not compile fpga so code maybe not work.
    [main.c, utils.c]
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2012-07-03 Fixing ADC read for the depth sensor without breaking accelerometer code.
2012-07-05 Stab at getting the shell to shell UI working. Write seems to work. Read doesn't and exiting results in a broken pipe.
    [utils.c]
2012-07-05 Prevent seg fault if ui is run with no process.
    [utils.c]
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2012-07-07 Fixing broken pipe, process kill problems. Now to attempt to read properly...
    [utils.c]
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2012-07-13 Adding missing interrupts file (oops).
    Changing the timer interrupt period into a #define rather than hard coding the period in hex.
    [main.c]
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2012-07-13 Fixing motor duty cycle PWM setting on the UI (multiply by a constant).
    [utils.c]
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2012-07-14 Fixing set depth function and adding capability to set depth from UI (dyn depth <target depth>).
    [main.c, utils.c]
2012-07-15 Fix bugs from water testing in PID controller code and UI. Still need to tune the P, I and D values from testing.
    [utils.c]
2012-07-16 Changed settings files to csv format due to auto text highlighting Added hough line finding filter and a class for storing lines easily
    [HSVFilter_settings.csv, HoughLines_settings.csv, camera_0_settings.csv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]
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2012-07-19 changed CV_GET_SEQ_ELEM back to cvGetSeqElem because former has errors. modified some settings for the netbook.
    [HSVFilter_settings.csv, HoughLines_settings.csv, common_settings.csv]
2012-07-22 Added mvCircles and mvHoughCircles for circle finding functionality. Added TriangularMatrix class and a test program to ensure to works properly.
    [HSVFilter_settings.csv, HoughCircles_settings.csv]
2012-07-23 Added first part of line clustering code. Removed TriangularMatrix class in favour or regular Matrix class because the matrix is not in fact triangular
    [HSVFilter_settings.csv, HoughCircles_settings.csv, HoughLines_settings.csv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]
2012-07-25 fixed some things for the motor linearization code. added proper equations to get the proper pwms (note: pwms are ints, and so the back motor pwm values add up to 1 less than the pwm of the front mot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
2012-07-26 Fix pwm_force.c so that it works as expected :D
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2012-07-28 Changed format of code. Class variables begin with underscore. Changed some settings to scale from img->width because that is the behavior we wanted in the old code. Differentiated these settings usi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
    [HSVFilter_settings.csv, HoughCircles_settings.csv, HoughLines_settings.csv]
2012-07-28 Some pwm code fix up.
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2012-08-02 more fixes
    [HSVFilter_settings.csv, HoughLines_settings.csv]
2012-08-03 Completed vision_new's clustering algorithm. Added gradient to webcam function (now works as intended). vision_new's webcam should be 1.5x to 2x faster than vision's
    [HSVFilter_settings.csv, HoughLines_settings.csv]
2012-08-03 Made fix to vision_new line clustering. Now validity is calculated using final cluster numbers. After more testing it turns out that vision_new doesnt have much performance boost over vision. On the 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
    [HSVFilter_settings.csv]
2012-08-04 Cleaned up mvClustering.cpp a lot. Implemented mvCanny. Used mvCanny in webcam to greatly reduce # of lines we will be expected to deal with. mvClustering has a bug were if nlines == nClusters then v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
    [gradient_settings.csv, test_settings.csv]
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2012-08-07 netbook fixes
    [HSVFilter_settings.csv, test_settings.csv]
2012-08-11 Added circle finding to webcam, changed gradient to a function from a class
    [gradient_settings.csv, test_settings.csv]
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2012-08-14 Put in min/max duty cycle guards. Fix up some #define stuff.
    [utils.c]
2012-08-24 Two minor enhancements: 1. print power failure when polling state (ie checking motor values) 2. ensure that target depth is set properly when turning on the controller.
    [utils.c]
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2012-08-28 Water testing changes - motor number hacks - tuned controller PID values - made motor signs correct
    [utils.c]
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2012-08-31 Added a vision module for testing purposes. Integrated into sim. However it does not work because it tries to find the settings files in the sim directory.
    [vision_module_test_settings.csv]
2012-08-31 Changed some settings in vision_module_test_settings so it actually works. Random fixes.
    [common_settings.csv, vision_module_test_settings.csv]
2012-09-08 Modified the way read_settings_file works so it looks for an env var first. Failing that it will use ./settings/ as the settings dir. Also fixed warnings in bmp_io.cpp
    [main.cpp]
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2012-09-15 Changed mvWebcam to not use a settings file since it is too simple to need to need one.
    [camera_settings.csv]
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2012-09-26 Fix typo, change RS232 device to Cyclone IVE.
2012-09-27 Modifications to the clustering routine. Now supports iteration > 1 and a better line diff metric (hopefully)
    [test_settings.csv]
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2012-09-28 Created base class for vision modules, base class and methods are used in the sim Added derived classes for each task. Users can add code to these classes in vision without touching sim.
    [vision_test_settings.csv]
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2012-10-01 Remove motor swap hack (swapping motor 0 and 2).
    [utils.c]
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2012-10-04 Fix IMU UART pins and add IMU reset to low.
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2012-10-05 Fix hex output to upper case.
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2012-10-05 Fix error printing for power interrupt and increase buffer size to prevent overflow.
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2012-10-18 Added prelim code for adaptive color filters. Also a settings file that I forgot.
    [vision_path_settings.csv]
2012-10-18 Fixed compile warnings on netbook (not on my comp somehow). Added profiling for functions. Added sample video.
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2012-10-21 Added FRAME module for the U shaped frame. Cleaned up mvBinaryMorphology. Added Open, Close, Gradient.
    [vision_frame_settings.csv]
2012-10-23 Add AquaTux class, main interface executable and a default aquatux settings file.
    [default_aquatux.csv]
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2012-10-25 Split init() functions used for FPGA and sim into init_fpga() and init_sim() to not cause linking problems. Added more meat to Simulator initialization.
    [main.cpp]
2012-10-25 Initialize sim and draw it (can't do anything to modify it yet though).
    [default_aquatux.csv]
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2012-10-26 Fix comment, return statement on main.
    [main.cpp]
2012-10-27 Fix header files. Allow way to recover stdin from sim loop (through pipe) to master thread.
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2012-10-28 Set up interface for ImageInput, that returns an image. Fix default aquatux settings. Hide write file from simulator.
    [default_aquatux.csv]
2012-10-28 Huge changes to dir structure. Moved vision modules to task, split .cpp into seperate files by task. Removed references to vision modules in sim. Changed vision modules to use static, not dynamically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
    [HSVFilter_settings.csv, HoughCircles_settings.csv, HoughLines_settings.csv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]
2012-10-28 Reproduce sim callbacks in interface sim. Trying to copy images from the sim...
    [default_aquatux.csv]
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2012-10-31 Add simulator commands to move in all directions and accelerate in all directions. Removing commands that aren't supported in the sim info message.
    [default_aquatux.csv]
2012-10-31 Make left and right turn instead of translate. Forward and reverse are now with respect to the current pitch. Also make sure that characters don't get printed to the ncurses window in joystick operat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
2012-11-02 Remove interface dependency from tasks.
    To do the video test, run ./aquatux ../settings/aquatux_video_test.csv (or just aquatux_video_test.csv).
    Also fixed some bugs in Aquatux.cpp.
    [aquatux_video_test.csv]
2012-11-03 Removed .deps from sim Makefile because it wont compile on Ritchie's comp. ImageInputVideo now works as intended.
    [aquatux_video_test.csv]
2012-11-03 Implemented SingleTaskMission, minor bugfixes
    [main.cpp]
2012-11-03 Fix Makefile archive targets so that static linking works when a lib*.a file is updated.
    Add destructors to everything in Aquatux.
    Trying out the new task stuff, segfaulting right now...
    [aquatux_task_test.csv]
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2012-11-05 Added other vision modules in JoystickOperation. Fixed settings files mappings for vision modules. Reverted to min_inter_cluster_diff in line clustering algorithm.
    [main.cpp]
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2012-11-06 Move around directory structure to allow for 'automatic' Makefiles. No more need to specify object files or dependencies! Just make sure to make deps if adding new files or new includes. Also, source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
    [main.cpp]
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2012-11-06 Changed #defines to static const char* for strings in vision modules. Added buoy module, but it doesnt seem to work so far.
    [vision_buoy_settings.csv, vision_gate_settings.csv]
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2012-11-08 Have IMU output working ~99% of the time. Doesn't have error detection though... This should be good enough to test controllers. Should be able to filter the 1% of errors pretty easily.
2012-11-08 Error check. IMU data should always be correct now.
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2012-11-09 Added attempts to program adaptive color filters. None of them work lol...
    [aquatux_video_test.csv, test_settings.csv]
2012-11-10 Update dependencies and ignore pitch when moving forward/reverse. Prevents a strange bug where moving forward may also move down because pitch isn't locked by a mutex and image-grabbing changes pitch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
2012-11-10 Give a way for the simulator to run tasks by passing control to the task until the task completes or a user quits the task by pressing 'q'.
    [aquatux_task_test.csv]
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2012-11-12 Added files needed for the 4 tasks we have vision modules for. Each task calls its vision module and can be selected in Aquatux.
    [vision_gate_settings.csv]
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2012-11-15 Fix target yaw past -180 and 180 degrees.
2012-11-15 Change depth units to cm. Moving target attitude accessors to attitude input. Fixed stop command to stop depth and yaw change.
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2012-11-16 Fix Makefile, make constants nicer for sim acceleration. Deleting fpga/ui dir since it was moved.
    [main.c, utils.c]
2012-11-16 Improve gate task.
    Instead of drifting yaw when we want to go forward, set the target yaw to the current yaw when going forward.
2012-11-17 Changed vision algorithms to run using a single 3-channel scratch image except for AdaptiveFilter3. Changed AdaptiveFilter3 to generate 2D histogram. Filter is still not done.
    [test_settings.csv]
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2012-11-27 Skip the buoy task and add it to the Mission. The mission can now reach the frame task, after skipping the buoy task.
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2012-11-30 Added mvAdvancedCircles, which will hopefully do a better job of finding circles than HoughCircles
    [test_settings.csv]
2012-12-01 Tune some parameters for less depth and yaw overshooting in the sim.
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2012-12-07 More updates to AdvancedCircles. Now better at detecting multiple circles (although you have to tune the parameters).
    [AdvancedCircles_settings.csv, vision_buoy_settings.csv]
2012-12-07 Add some comments to the aquatux config file, the top-level class and main.
    [default_aquatux.csv]
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2012-12-10 Add options to display image stream (ie from webcam or video) and to record videos of the image stream (ie sim or webcam). Video writing is still a bit buggy (images are reversed), but they show exac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
    [aquatux_video_test.csv, default_aquatux.csv]
2012-12-10 Allow display of raw image stream input (ie webcam or video) in openCV windows. Forward and Down images are displayed in different windows. Also adding a webcam settings file.
    [aquatux_video_test.csv, aquatux_webcam_test.csv, default_aquatux.csv]
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2012-12-13 Remove img->origin = 1 code. The sim will properly flip the image so that the origin is 0 (top-left). I also had to change the direction of the path code, based on the angle.
    Path angle returned from image: negative if /, positive if \
    Therefore, the sub should turn LEFT by the angle returned. ie, if \, then sub should turn left, and if /, the sub should turn right.
    This should mean that the control/vision code works the same on images given by the sim, webcam or videos. Previously, the sim images would be filtered with a vertical flip, changing the value of the angles returned of lines.
    [aquatux_sim_playback_test.csv]
2012-12-13 Remove y < 0 to case in vision_path to fix atan. It's hard to tell if we should move more than 180 degrees to align with a path, so assume it's pointing in the right direction.
2012-12-13 Try to improve responsiveness of sim's dynamics. Remove hack from path task and fix possible race condition in the simulator thread.
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2012-12-14 Implement proper thread termination for the sim. May help resolve segfaults when exiting.
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2012-12-18 Adds buoy vision module. Differentiates between readying and getting image in ImageInput. This allows tasks to refresh the camera buffer (fast) without retreiving a frame it doesn't use (slow).
    [aquatux_video_test.csv]
2012-12-18 Adding some missing PCB files, and cleaning up the directory a bit. Put in the skeleton prototype sonar board project
    [Motor Driver 6 Element.brd, Motor Driver 6 Element_Feb2012.brd, Motor Driver 6 Element_Feb2012.sch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]
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2012-12-20 Fixed error in vision/webcam due to settings for AdvancedCircles Added basic task_buoy - calculation of range seems very off and cant handle depth differences yet Added line to kill a task module if 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
    [test_settings.csv]
2012-12-21 Fixed range issue in vision_buoy - was confusing diameter and radius Fixed depth adjustment in task_buoy Reduced target depth in task_path - if we sink too low the path wont fit in the image and that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
    [vision_buoy_settings.csv]
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2013-01-06 Fixes the OpenCV assert errors in cvCvtColor - the problem was due to the images having non-identical dimensions.
    [main.cpp]
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2013-01-24 Fix script in case the numbers alias...
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2013-01-26 adaptive filter fixes!
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2013-02-02 fixed PID controller
2013-02-02 Undo PID usage in the sim (doesn't work yet).
    Fix compile and change headers.
2013-02-03 Fix PID and use it in the sim (try some new params).
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2013-02-09 Fixes bugs in MeanShift and adjust webcam settings.
    [test_settings.csv]
2013-02-09 Revert sim PID controller constants to a decent value (tuned for netbook).
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2013-02-20 Minor changes to interface and differentiate between powering on and the startup sequence (power on will enable IMU readings, startup sequence activates all controllers to stabilize attitude).
    [main.c]
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2013-03-05 Add settings file for submarine and update code to prevent seg faults when nios2-terminal is not on your path.
    [aquatux_submarine.csv]
2013-03-10 Fixed path code to reliably track one path or the other. There are currently a lot of seg faults, and I am unsure if this is my code, my platform, the other code, or some combination of all of them. 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
2013-03-16 Fix yaw controller at -180/+180 border.
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2013-03-19 Try to fix pitch problem (wrong place to put semaphore up). Also add starting locations for marker dropper and torpedo target.
    [sim.csv]
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2013-03-25 Added color checking capability to mvCircle and mvRect. Debugged problems with color infrastructure.
    [main.cpp]
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2013-04-05 Move calculate_pid() out of interrupt handler so it doesn't compete with more important interrupts such as power management and getting data from the IMU.
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2013-04-06 This should fix slow webcam update on the netbook. Poll more often for the image (200 Hz), but at a different rate as attitude input (10 Hz).
2013-04-06 Reverted buoy task to only look for and target the circular buoy. Can use this for April water test.
    [sim.csv, vision_buoy_settings_new.csv]
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2013-04-07 Move controller debug out of calculate_pid so that it can optionally be called when polling attitude. Split update_depth_reading() out of calculate_pid(), since that short piece of code will remain i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
    [main.c]
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2013-04-16 Fix 2 webcam problem. Use a smaller capture frame to reduce USB bandwidth. 400x300 or 320x240 work. 640x480 does not fit.
2013-04-17 Reverts some files so tasks work properly in simulator
    [vision_buoy_settings_new.csv, vision_path_settings.csv, vision_test_settings.csv]
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2013-04-19 Fix > 180 case for Hue.
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2013-04-28 Try to exit gracefully (power down) if experiencing a seg fault or if an SSH connection dropped (may not work immediately).
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2013-04-29 Minor changes to UI. Doesn't work for setting individual motors.
    [main.c]
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2013-05-04 Fixes debug messages in vision and task + further cleans up some code.
    [test_settings.csv]
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2013-05-04 More updates to color filtering + fix a bug in binary dilate
    [test_settings.csv]
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2013-05-30 Adds some error checks to vision modules. Puts DIFF_THRESHOLD into settings file.
    [sim.csv, vision_buoy_settings_new.csv, vision_path_settings.csv]
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2013-05-31 Revert sim settings.
    [sim.csv]
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2013-07-06 1. Adds new option to WaterShed to seed more densely - using this now. 2. Fixes large scale bug in mvContours where only the first contour in a chain is analyzed. 3. Changes how circles/rboxes are ad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
2013-09-27 Change static libraries to dynamic libraries. Should mean less recompiling, but still proper dependencies met with compiling. If it doesn't work, just revert.
    [main.cpp]
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2013-11-23 Added some more missing sonar board files.
    [sonar_board_rev_2013A.PrjPcb, sonar_board_rev_2013A.SchDoc]
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2014-02-23 Adding a couple missing precompiled libraries.
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2014-05-23 added new main stack connector footprint, resolved headaches
    [Sonar_board.PcbDoc, main_stack_dual_channel.SchDoc, power_management.SchDoc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]
2014-05-25 added holes for standoffs and positioned main connectors correctly
    [Sonar_board.PcbDoc]
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2014-06-06 first iteration placement for pre-amp, a few netlist fixes
    [Sonar_board.PcbDoc]
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2014-06-07 Added a couple of BoMs and a digikey receipt for older boards. Missing a BoM for the IF board
    [Motor_Boards_BoM_v1.xls, PowerManagementBoard_BoM.xls]
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2014-06-19 tightened component positioning, dealt with most design violations, and moved rooms around so channels get equal access to ADC and buffer
    [Sonar_board.PcbDoc]
2014-06-24 fixed misplacement of components in one channel, going to try some routing to test copying between rooms
    [Sonar_board.PcbDoc]
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2014-11-24 Pair A almost complete, fixed some wonky vias
    [Sonar_board.PcbDoc]
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
